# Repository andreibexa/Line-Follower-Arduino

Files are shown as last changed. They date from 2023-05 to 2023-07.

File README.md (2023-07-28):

# Line-Follower-Arduino
An Arduino-based line follower robot that autonomously tracks and follows a predefined path, controlled with Arduino Cloud.
Read more details in [Project_overview.pdf](https://github.com/andreibexa/Line-Follower-Arduino/blob/main/doc/Line%20follower%20wiring%20schematic.pdf)

## Main functionalities:
1. Line Follower
2. Line obstacle avoider
3. Communication between 2 microcontrollers
4. WiFi Manager
5. Configuration and control through Arduino Cloud
6. Saving configuration to EEPROM
7. Push button - Line Follower start/stop
8. LCD Display:
9. RSSI - WiFi signal strength
10. Cloud status
11. 18650 battery voltage
12. AA batteries voltage
13. RGB LED for: WiFi, Cloud, and Line Follower status
14. Buzzer
15. On/off button

## Diagram
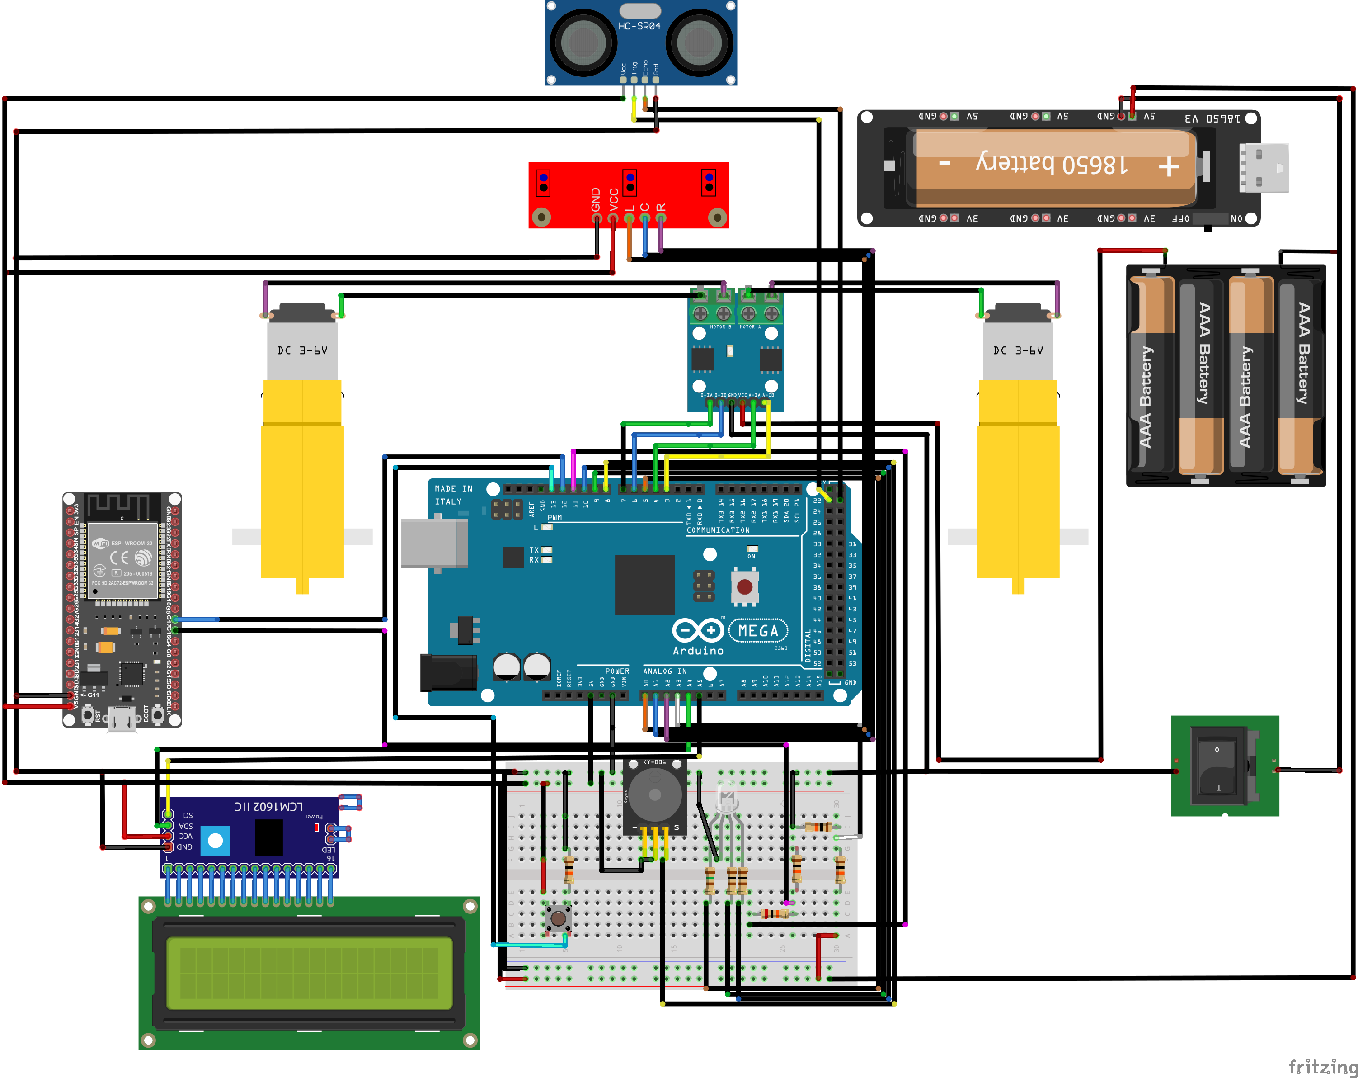
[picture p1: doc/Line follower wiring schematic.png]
Line follower diagram


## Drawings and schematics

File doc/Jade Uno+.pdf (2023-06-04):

# GroundStudio Jade Uno+

## ISP Port

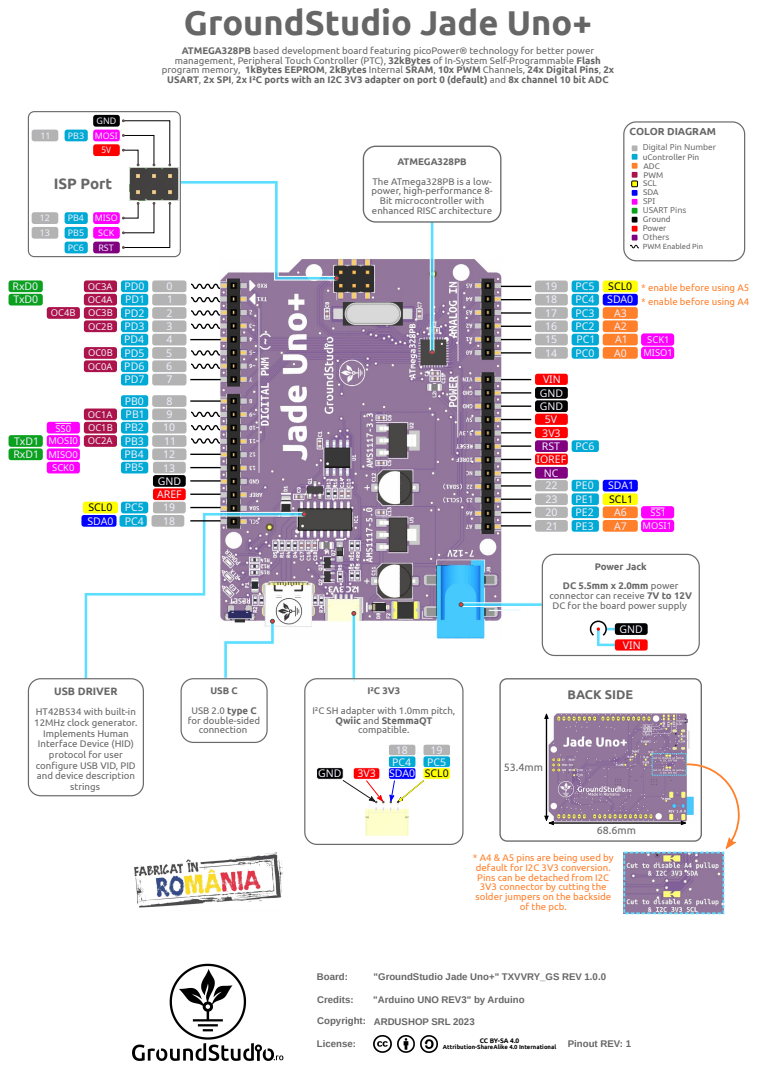
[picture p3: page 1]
Board:; Credits:; "Arduino UNO REV3" by Arduino; Copyright:; License:; ARDUSHOP SRL 2023; Pinout REV: 1; * enable before using A5; * enable before using A4; SDA0; SCL0; GND MOSI 5V; PB5 SCK; MISO; RST; MISO0; TxD0; RxD0; SCK0; AREF; GND; VIN; RST PC6; IOREF; USB DRIVER; strings; I²C 3V3; GND 3V3; SDA1 SCL1; MOSI0; TxD1 RxD1; MISO1; MOSI1; SCK1; BACK SIDE

ATMEGA328PB based development board featuring picoPower® technology for better power
management, Peripheral Touch Controller (PTC), 32kBytes of In-System Self-Programmable Flash
program memory, 1kBytes EEPROM, 2kBytes Internal SRAM, 10x PWM Channels, 24x Digital Pins, 2x
USART, 2x SPI, 2x I²C ports with an I2C 3V3 adapter on port 0 (default) and 8x channel 10 bit ADC

COLOR DIAGRAM
Digital Pin Number
uController Pin
ADC
PWM
SCL
SDA
SPI
USART Pins
Ground
Power
Others
PWM Enabled Pin

ATMEGA328PB
The ATmega328PB is a low-
power, high-performance 8-
Bit microcontroller with
enhanced RISC architecture

Power Jack
DC 5.5mm x 2.0mm power
connector can receive 7V to 12V
DC for the board power supply

USB C
USB 2.0 type C
for double-sided
connection

HT42B534 with built-in
12MHz clock generator.
Implements Human
Interface Device (HID)
protocol for user
configure USB VID, PID
and device description

I²C SH adapter with 1.0mm pitch,
Qwiic and StemmaQT
compatible.
SDA0 SCL0

* A4 & A5 pins are being used by
default for I2C 3V3 conversion.
Pins can be detached from I2C
3V3 connector by cutting the
solder jumpers on the backside

of the pcb.

"GroundStudio Jade Uno+" TXVVRY_GS REV 1.0.0

Attribution-ShareAlike 4.0 International

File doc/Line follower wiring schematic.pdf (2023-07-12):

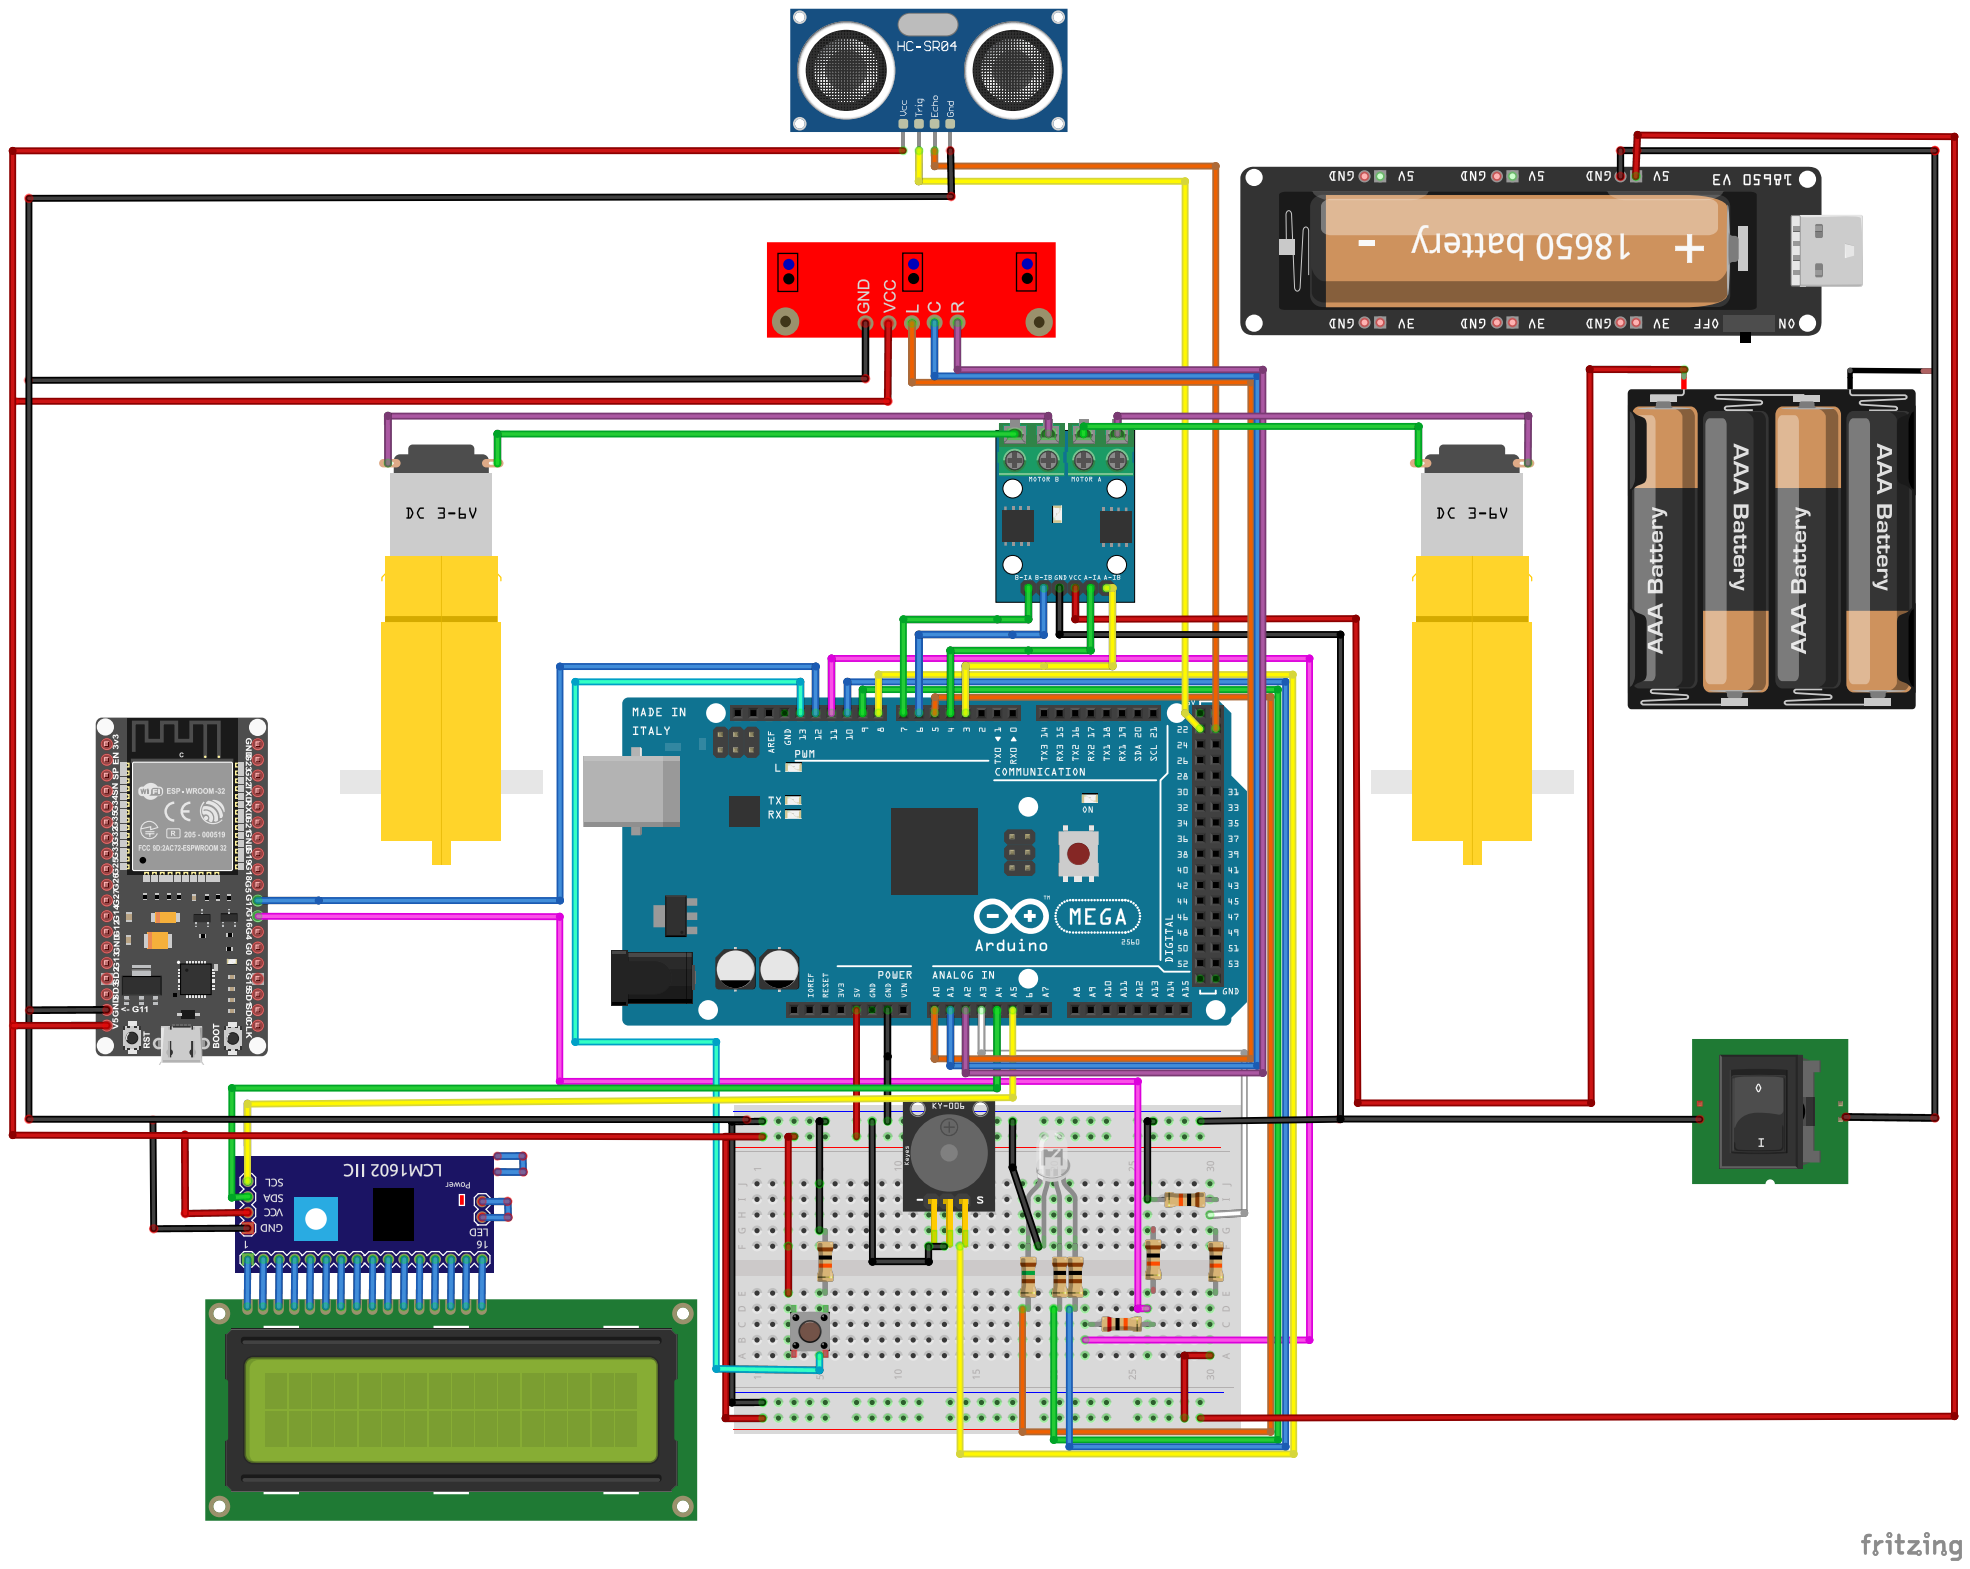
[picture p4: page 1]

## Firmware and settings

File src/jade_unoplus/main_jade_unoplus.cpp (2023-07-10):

#include <Arduino.h>
#include "jade_unoplus/line_follower/line_follower.h"
#include "jade_unoplus/eeprom_data/eeprom_data.h"
#include "jade_unoplus/jade_transfer/jade_transfer.h"
#include "jade_unoplus/line_follower/button_mode.h"
#include "jade_unoplus/multicolor_led/multicolor_led.h"
#include "jade_unoplus/pins_jade_unoplus.h"
#include "jade_unoplus/lcd/lcd.h"
#include "jade_unoplus/system_status/system_status.h"

/**
 * @brief Set pin mode for the Jade Uno+ board
 *
 */
void setPinsMode() {
  // Dual-Channel H-Bridge Motor Driver Module
  pinMode(MOTOR_RIGHT_FORWARD_PIN, OUTPUT);
  pinMode(MOTOR_RIGHT_BACKWARD_PIN, OUTPUT);
  pinMode(MOTOR_LEFT_FORWARD_PIN, OUTPUT);
  pinMode(MOTOR_LEFT_BACKWARD_PIN, OUTPUT);

  // IR Infrared Line Follower Sensor Module
  pinMode(IR_TRACKING_SENSOR_LEFT_PIN, INPUT);
  pinMode(IR_TRACKING_SENSOR_CENTER_PIN, INPUT);
  pinMode(IR_TRACKING_SENSOR_RIGHT_PIN, INPUT);

  // Ultrasonic Sensor Module
  pinMode(ULTRASONIC_TRIG_PIN, OUTPUT);
  pinMode(ULTRASONIC_ECHO_PIN, INPUT);

  // Multicolor led
  pinMode(RED_PIN, OUTPUT);
  pinMode(GREEN_PIN, OUTPUT);
  pinMode(BLUE_PIN, OUTPUT);

  // Buzzer
  pinMode(BUZZER_PIN, OUTPUT);

  // Line follower pushup button (On/Off)
  pinMode(LINE_FOLLOWER_BUTTON_PIN, INPUT);
}

/**
 * @brief Arduino setup function
 *
 */
void setup() {
  // Put your setup code here, to run once:
  Serial.begin(115200);

  // Set the pins mode
  setPinsMode();

  // Initialize EEPROM
  initializeEEPROM();

  // Serial Transfer setup
  setupSerialTransfer();

  // LCD setup
  setupLCD();

  // System status setup
  setupSystemStatus();
}

/**
 * @brief Arduino main loop
 *`
 */
void loop() {
  // Multicolor LED loop
  loopMultiColorLed();

  // Serial Transfer loop
  loopSerialTransfer();

  // Debounce the line follower mode on button pushup
  debounceLineFollowerButton();

  // Line follower loop
  loopLineFollower();

  // System status loop
  loopSystemStatus();
}

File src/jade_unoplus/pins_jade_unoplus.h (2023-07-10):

#ifndef JADE_UNOPLUS_PINS_JADE_UNOPLUS_H_
#define JADE_UNOPLUS_PINS_JADE_UNOPLUS_H_

#include <Arduino.h>


// Push up button to change line follower mode (On/Off)
#define LINE_FOLLOWER_BUTTON_PIN 2

// Dual-Channel H-Bridge Motor Driver Module - L9110S
#define MOTOR_RIGHT_FORWARD_PIN 3   // M1(A) - PWM PIN
#define MOTOR_RIGHT_BACKWARD_PIN 4  //  M1(B)

#define MOTOR_LEFT_FORWARD_PIN 6   // M2(A) - PWM PIN
#define MOTOR_LEFT_BACKWARD_PIN 7  // M2(B)

// Buzzer
#define BUZZER_PIN 8  // PWM PIN

// Multicolor led
#define RED_PIN 5    // RED - PWM PIN
#define GREEN_PIN 9  // GREEN - PWM PIN
#define BLUE_PIN 10  // BLUE - PWM PIN

// Serial RX and TX
#define TX_PIN 11  // TX PIN
#define RX_PIN 12  // RX PIN

// Ultrasonic Sensor Module - HC-SR04
#define ULTRASONIC_TRIG_PIN 22  // TRIG
#define ULTRASONIC_ECHO_PIN 23  // ECHO

// 3 Channel Red IR Infrared Tracking Sensor Module - CTRT5000
#define IR_TRACKING_SENSOR_LEFT_PIN A0    // OTL
#define IR_TRACKING_SENSOR_CENTER_PIN A1  // OTC
#define IR_TRACKING_SENSOR_RIGHT_PIN A2   // OTR

// AA Battery voltage divider
#define AA_BATTERY_VOLTAGE_PIN A3

// LCD Display 1602 + I2C
#define LCD_SDA_PIN A4  // SDA
#define LCD_SCL_PIN A5  // SCL

#endif  // JADE_UNOPLUS_PINS_JADE_UNOPLUS_H_

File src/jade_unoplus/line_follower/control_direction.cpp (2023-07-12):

#include "jade_unoplus/line_follower/control_direction.h"

/**
 * @brief Control the direction and speed of both wheels for a specific period
 *
 * @param direction Movement direction
 * @param speed Movement speed (0-255)
 * @param runTime Running period in ms. Default 1000ms
 */
void temporizedDirection(uint8_t direction, uint8_t speed, int16_t runTime = 1000) {
  static uint32_t startTime = millis();
  uint32_t currentTime = millis();

  speed = constrain(speed, 0, 255);

  while (currentTime - startTime < abs(runTime)) {
    setDirection(direction, speed);

    if (runTime == 0) {
      break;
    }

    // Update current time
    currentTime = millis();
  }
}

/**
 * @brief Control the direction and speed of both wheels
 *
 * @param direction Movement direction
 * @param speed Movement speed (0-255)
 *
 */
void setDirection(uint8_t direction, uint8_t speed) {
  speed = constrain(speed, 0, 255);

  uint8_t calibrateLeft = 255;
  uint8_t calibrateRight = 220;
  uint8_t leftSpeed = map(speed, 0, 255, 0, calibrateLeft);
  uint8_t rightSpeed = map(speed, 0, 255, 0, calibrateRight);

  switch (direction) {
    // FORWARD
    case FORWARD:
      analogWrite(MOTOR_LEFT_FORWARD_PIN, leftSpeed);
      digitalWrite(MOTOR_LEFT_BACKWARD_PIN, LOW);
      analogWrite(MOTOR_RIGHT_FORWARD_PIN, rightSpeed);
      digitalWrite(MOTOR_RIGHT_BACKWARD_PIN, LOW);
      break;
    // BACKWARD
    case BACKWARD:
      digitalWrite(MOTOR_LEFT_FORWARD_PIN, LOW);
      analogWrite(MOTOR_LEFT_BACKWARD_PIN, leftSpeed);
      digitalWrite(MOTOR_RIGHT_FORWARD_PIN, LOW);
      analogWrite(MOTOR_RIGHT_BACKWARD_PIN, rightSpeed);
      break;
    // RIGHT WIDE FORWARD
    case RIGHT_WIDE_FORWARD:
      analogWrite(MOTOR_LEFT_FORWARD_PIN, leftSpeed);
      digitalWrite(MOTOR_LEFT_BACKWARD_PIN, LOW);
      digitalWrite(MOTOR_RIGHT_FORWARD_PIN, LOW);
      digitalWrite(MOTOR_RIGHT_BACKWARD_PIN, LOW);
      break;
    // RIGHT TIGHT FORWARD
    case RIGHT_TIGHT_FORWARD:
      analogWrite(MOTOR_LEFT_FORWARD_PIN, leftSpeed);
      digitalWrite(MOTOR_LEFT_BACKWARD_PIN, LOW);
      digitalWrite(MOTOR_RIGHT_FORWARD_PIN, LOW);
      analogWrite(MOTOR_RIGHT_BACKWARD_PIN, rightSpeed);
      break;
    // RIGHT WIDE BACKWARD
    case RIGHT_WIDE_BACKWARD:
      digitalWrite(MOTOR_LEFT_FORWARD_PIN, LOW);
      analogWrite(MOTOR_LEFT_BACKWARD_PIN, leftSpeed);
      digitalWrite(MOTOR_RIGHT_FORWARD_PIN, LOW);
      digitalWrite(MOTOR_RIGHT_BACKWARD_PIN, LOW);
      break;
    // LEFT WIDE FORWARD
    case LEFT_WIDE_FORWARD:
      digitalWrite(MOTOR_LEFT_FORWARD_PIN, LOW);
      digitalWrite(MOTOR_LEFT_BACKWARD_PIN, LOW);
      analogWrite(MOTOR_RIGHT_FORWARD_PIN, rightSpeed);
      digitalWrite(MOTOR_RIGHT_BACKWARD_PIN, LOW);
      break;
    // LEFT TIGHT FORWARD
    case LEFT_TIGHT_FORWARD:
      digitalWrite(MOTOR_LEFT_FORWARD_PIN, LOW);
      analogWrite(MOTOR_LEFT_BACKWARD_PIN, leftSpeed);
      analogWrite(MOTOR_RIGHT_FORWARD_PIN, rightSpeed);
      digitalWrite(MOTOR_RIGHT_BACKWARD_PIN, LOW);
      break;
      // LEFT WIDE BACKWARD
    case LEFT_WIDE_BACKWARD:
      digitalWrite(MOTOR_LEFT_FORWARD_PIN, LOW);
      digitalWrite(MOTOR_LEFT_BACKWARD_PIN, LOW);
      digitalWrite(MOTOR_RIGHT_FORWARD_PIN, LOW);
      analogWrite(MOTOR_RIGHT_BACKWARD_PIN, rightSpeed);
      break;
    // STOP FAST
    case STOP_FAST:
      digitalWrite(MOTOR_LEFT_FORWARD_PIN, HIGH);
      digitalWrite(MOTOR_LEFT_BACKWARD_PIN, HIGH);
      digitalWrite(MOTOR_RIGHT_FORWARD_PIN, HIGH);
      digitalWrite(MOTOR_RIGHT_BACKWARD_PIN, HIGH);
      break;
    // STOP SLOW
    case STOP_SLOW:
    default:
      digitalWrite(MOTOR_LEFT_FORWARD_PIN, LOW);
      digitalWrite(MOTOR_LEFT_BACKWARD_PIN, LOW);
      digitalWrite(MOTOR_RIGHT_FORWARD_PIN, LOW);
      digitalWrite(MOTOR_RIGHT_BACKWARD_PIN, LOW);
  }
}

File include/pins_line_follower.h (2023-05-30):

#ifndef PINS_LINE_FOLLOWER_H_
#define PINS_LINE_FOLLOWER_H_

#include <Arduino.h>

// Dual-Channel H-Bridge Motor Driver Module - L9110S
#define MOTOR_RIGHT_FORWARD_PIN 5  // M1(A) - PWM PIN
#define MOTOR_RIGHT_BACKWARD_PIN 6 //  M1(B) - PWM PIN

#define MOTOR_LEFT_FORWARD_PIN 9   // M2(A) - PWM PIN
#define MOTOR_LEFT_BACKWARD_PIN 10 // M2(B) - PWM PIN

// 3 Channel Red IR Infrared Tracking Sensor Module - CTRT5000
#define IR_TRACKING_SENSOR_RIGHT_PIN 11  // OTL
#define IR_TRACKING_SENSOR_CENTER_PIN 12 // OTC
#define IR_TRACKING_SENSOR_LEFT_PIN 13   // OTR

// Ultrasonic Sensor Module - HC-SR04
#define ULTRASONIC_TRIG_PIN 2 // TRIG
#define ULTRASONIC_ECHO_PIN 3 // ECHO
#endif                        // PINS_LINE_FOLLOWER_H_

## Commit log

2023-05-16 Add line follower wiring schematic
    [Line follower wiring schematic.fzz]
2023-05-16 Rename PIN names
2023-05-16 Add running DC motor "A"
2023-05-17 ADD DC motors and batteries
    [Line follower wiring schematic.fzz]
2023-05-17 Add IR Infrared Line Follower Sensor
    [Line follower wiring schematic.fzz]
2023-05-17 ADD IR Infrared sensors
2023-05-18 MOVE IR pins to Analog pins
    [Line follower wiring schematic.fzz]
2023-05-18 CHANGE pins for IR sensor
2023-05-18 CREATE base function to control DC motors
2023-05-19 FAILED to implement PID control algorithm
    [Line follower wiring schematic.fzz]
2023-05-22 Test with PID algorithm
2023-05-23 FAILED to set PID
    [Line follower wiring schematic.fzz]
2023-05-23 another PID failure
2023-05-27 Line follower with PID
2023-05-29 ADD ultrasonic sensor pins
2023-05-29 SET ultrasonic sensor pins
2023-05-30 REMOVE Serial.print(FCPU)
2023-05-30 UPDATE comments for IR tracking sensor pins
2023-05-31 Avoid obstacle 😠
2023-06-04 ADD Arduino Cloud
2023-06-06 ADD Led matrix 8x8
2023-06-12 ADD CPPLINT.cfg
    [CPPLINT.cfg]
2023-06-12 ADD Led matrix module
2023-06-13 FIX the stop line follower command sent from Arduino cloud
    [line_follower.cpp]
2023-06-13 Remove the Led Matrix
2023-06-13 ADD pushup button to turn on or off the line follower
2023-06-14 ADD MultiColor LED
2023-06-27 FIX Read AA battery voltage
    [battery_voltage.cpp, pins_jade_unoplus.h]
2023-06-28 ADD Buzzer pin
2023-06-29 REMOVE Async timer library
2023-06-29 ADD Buzzer module with tones
    [line_follower.cpp, main_jade_unoplus.cpp, pins_jade_unoplus.h]
2023-07-03 ADD ESP32
    [Line follower wiring schematic.fzz]
2023-07-04 ADD voltage divider
    [Line follower wiring schematic.fzz]
2023-07-04 REMOVE Serial print
2023-07-04 REPLACE Switch
    [Line follower wiring schematic.fzz]
2023-07-06 CHANGE LCD position
    [Line follower wiring schematic.fzz]
2023-07-06 ADD Wiring schematic as pdf
2023-07-10 Fix multiple issues. Fix ESP32 int transfer to Jade UnoPlus
    [battery_voltage.cpp, line_follower.cpp, main_jade_unoplus.cpp]
2023-07-10 Increase ESP32 partition size
2023-07-10 Remove Serial.print
2023-07-12 CALIBRATE Right motor
    [Line follower wiring schematic.fzz]
2023-07-28 ADD wiring schematic as png
